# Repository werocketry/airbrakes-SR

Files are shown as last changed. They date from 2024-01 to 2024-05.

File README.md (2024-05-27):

# airbrakes-SR

This is the repository for the Western Engineering Rocketry Team's design of an airbrakes system.

## Sister Projects

- [werocketry/RocketFlightSim](https://github.com/werocketry/RocketFlightSim)
- [werocketry/HPR-Rocket-Flight-Computer](https://github.com/werocketry/HPR-Rocket-Flight-Computer)

## Acronyms of the Trade
| Acronym | Full Name | Description |
|---|---|---|
| AGL | Above Ground Level | |
| COTS | Commercial off-the-shelf | |
| CP | Center of pressure | |
| ESRA | Experimental Sounding Rocket Association  | |
| FOS | Factor of Safety | |
| FS | Factor of Safety | |
| IREC | Intercollegiate Rocket Engineering Competition | Basically SAC. It used to happen somewhere else |
| NM | New Mexico | |
| NMSU | New Mexico State University | The university on whose grounds some parts of SAC are held |
| OR | OpenRocket | |
| .ork | OpenRocket filetype | |
| RSO | Range Safety Officer | The person that gives you permission to launch |
| SA | Spaceport America | The launch site where SAC is hosted |
| SAC | Spaceport America Cup | |
| SRAD | Student researched and designed | |
| VLA | Vertical Launch Area | |
| WERT | Western Engineering Rocketry Team | Also called WE Rocketry |

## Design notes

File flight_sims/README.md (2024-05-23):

# Flight Analysis

Flight simulations, analysis of Prometheus' flight data

- **Alignment of Sim Data with Experimental Data:** 
  - About 1000 ft off around motor burnout.
  - try taking data to motor burnout and simulating remainder of flight to see congruence with experimental data
    - just run sim as is and set deployment angle to 0 for the entire flight
  - this isn't a real problem; it's caused by the delay in barometric sensor data. The rocket should have been just about where the sim says it would be at motor burnout, it's just a delay on the order of 0.8s in the pressure in the rocket getting to equilibrate with the pressure outside the rocket that causes the discrepancy.
  - Note that if wanting to simulate airbrakes using Prometheus experimental data as the data till burnout, the flight data has no vertical vs horizontal velocity data, so would need to use the speed and change of height with time to separate them out. Possibly use the velocity not being 0/the acceleration not being -g at apogee to help determine the horizontal motion then too. Not a priority at all.

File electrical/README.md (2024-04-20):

# Electrical 
TODO

## Future Work
### Electrical Hardware Revision

Future work will also focus on the revision of the electrical hardware,
namely the manufacture and testing of the printed circuit board for the
presented Production Prototype version of the electrical system.

### Flight Computer Development

As the development of a complete flight computer is a large undertaking,
future development is required to satisfy this component. The team will
work closely with the sponsor to ensure that our development efforts run
parallel to their future development of SRAD flight computers.

### Software Integration

The core software components of the system presented complete herein
still require careful development and planning for their integration
into a single standalone program capable of running this entire complex
system.

### Model-Based Control for Drag Modulation

The current mechanism controller uses a look up table calculated offline
to determine the motor action required to produce the desired drag.
Future work will focus on the use of a Model Prediction Control
algorithm which uses an internal model of the rocket to predict the path
and actively mitigate deviations from the desired path in the presence
of external disturbances.

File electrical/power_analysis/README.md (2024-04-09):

The power supply for the project relies on Lithium-ion (Li-ion) batteries, selected for their high energy density and efficiency. The choice of Li-ion batteries was heavily influenced by competition rules that explicitly ban the use of Lithium Polymer (LiPo) batteries \[4\] and our research showed that this is a common alternative used in the SAC competition. In selection of the battery cells the capacity, max discharge rate, and voltage requirements were considered. The power consumption ratings for each of the relevant components is given in Table 1.

**Table 1: Power Consumption of Relevant Electrical Components.**

| Component | Electrical Power | Details |
|---|---|---|
| Portenta H7 | 2.6 mA @ 3.7V | Current consumption in busy loop (@5V) \[max with on board LEDs off\]. |
| Nicla Sense ME | 2.5 mA @ 3.7V | Power consumption advertising with sensor polling at 1Hz \[max consumption state\]. |
| L298N Motor Driver (VEN=L)  | 4 mA @ 12V<br>6mA @ 5V | Quiescent supply & VSS current of inactive driver \[max value of range taken\]. |
| L298N Motor Driver (VEN=H)  | 22 mA @ 12V<br>36 mA @ 12V | Quiescent supply & VSS current of active driver \[max value of range taken\]. |
| Brushed DC Motor | 5000 mA @ 12V | Stall current of the selected motor. |
| Hall Effect Sensor | 6.9 mA @ 5V | Supply current of the IC. |

To calculate the required capacity, the 20-hour required standby time given in ER-003 and an active motor time of 10 seconds (approximately a FOS of double the predicted motor action time. This yields a total required capacity of approximately 400 mAh, the calculations are broken down in Table 2. The datasheet for the Arduino Portenta recommends a greater minimum of 700 mAh for battery powered use and this will hence be used as the single cell minimum herein.

**Table 2: Energy Requirement Breakdown.**

| Phase | Component | Current (mA) | Voltage (V) | Active Time | Energy Required (mAh) |
|---|---|---|---|---|---|
| Standby | Portenta H7 | 2.6 | 3.7 | 20h | 52 |
| | Nicla Sense ME | 2.5 | 3.7 | 20h | 50 |
| | L298N Motor Driver | 6 | 5 | 20h | 120 |
| | Hall Effect Sensor | 6.9 | 5 | 20h | 138 |
| Standby Subtotal | | | | | 360 |
| Active | Brushed DC Motor | 5000 | 12 | 20s | 27.78 |
| | L298N Motor Driver (Active) | 36 | 12 | 20s | 0.2 |
| Active Subtotal | | | | | 27.98 |
| **Total Required Energy** | | | | | 387.98 |

The MCU board is supplied with by a single 3.7V cell which the onboard regulator regulates to 5V to power the 5V components. The DC motor is rated at 12V therefore 3 cells are required to reach the required potential which results in a nominal 11.1V (within 10%). As the cells will be wired in a 3 series (3S) configuration each must independently be capable of supplying the maximum current of the motor, that is 5000 mA which sets the required minimum discharge current.

This gives a selection criterion of three cells rated at least 700 mAh each with a minimum discharge rate of 5000 mA. The Panasonic NCR18650GA 3450mAh 10A Battery was chosen for this application as it meets and exceeds these required specifications while remaining well within budget. It's important to note that most modern lithium-ion cells, even those that are more affordably priced, meet or exceed the required specifications for this project making the exact product selection rather arbitrary. Therefore, the specific selection of the product was primarily driven by the reputable brand name, price point, and supplier accessibility. The power to the microcontroller uses the same model of low-power switch as for the user input and the power switch to enable power to the motor circuit is a power switched rated up to 6A.

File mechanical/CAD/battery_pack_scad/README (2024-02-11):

https://www.amazon.ca/0-15x6x50mm-Soldering-Capacity-Lithium-Battery/dp/B07PQP55CM?th=1

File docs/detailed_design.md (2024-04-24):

# Detailed Design

## Mechanical Design

After the transition to three flaps in January, the basic mechanical
design has remained largely unchanged, barring a few minor, yet
necessary, adjustments identified through the mechatronic model. The
initial modification involved adding washers at both ends of the lead
screw, addressing rough edges (burrs) left from the lathe-milling
process. To accommodate the lead screw\'s turned-down smooth shaft, and
ensure an effective interface with the bronze bearing, two precision
tolerance washers from McMaster-Carr were selected, as detailed in
Figure 13. Another revision was the development of a motor mount. The
integration of electronic components revealed the absence of a suitable
motor mounting solution on the top platform and lead screw. To solve
this, a component that attaches to the top platform was designed,
providing a robust mount for the motor and facilitating the coupler
connection to the lead screw, depicted in Figure 16.

The third modification entailed adding three \"platform spacers\" to
maintain the critical distance between the two platforms, which directly
influences the compression on the lead screw. Too little distance
results in binding due to the lead screw pressing against the platforms,
while too much distance introduces unwanted play in the mechanism. The
incorporation of these spacers, firmly secured with screws, ensures the
correct spacing is consistently maintained, highlighted in blue in
[]{.mark}Figure 14. This approach was deemed suitable as it had been
effectively tested in the 3D-printed mechatronic model and the
airbrake\'s weight budget comfortably accommodated the additional mass.

Initially, the correct spacing was to be achieved by first installing
the top platform, measuring the appropriate distance, then fitting the
remainder of the system. However, recognizing the potential for
variability in this method, it was decided to include platform spacers
to allow for one-piece installation, enhancing precision and
reliability.

Subsequent adjustments were made to the flap dimensions, following the
WE Rocketry Team\'s recommendation for slightly larger flaps. This
necessitated minor modifications to maintain the correct part
relationships, preserving the mechanism\'s fundamental operation as
established in previous iterations.

Finally, the integration of electronics prompted the addition of Hall
Effect sensors to determine the system\'s limits, requiring alterations
to accommodate sensor boards on the top and bottom platforms and the
installation of magnets on the lead nut. These changes, though minor,
were crucial for the precise functioning of the mechanism, illustrated
in Figure 15.

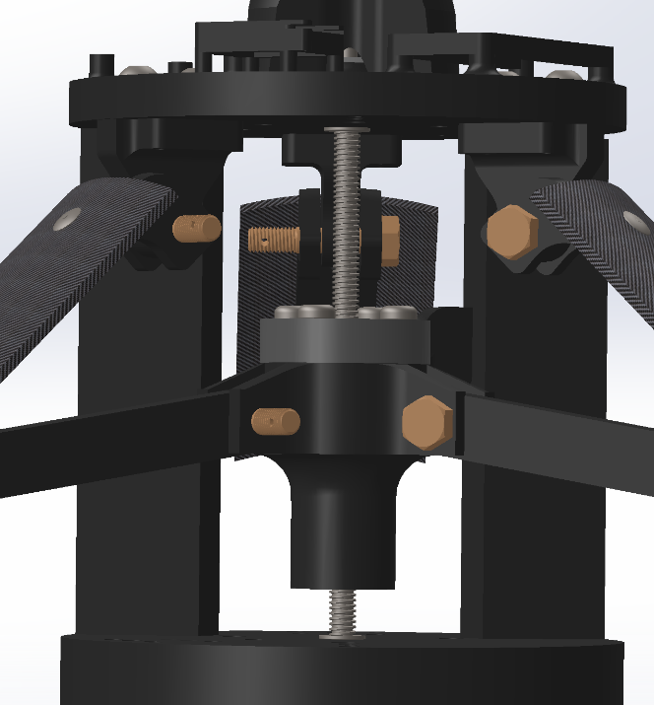
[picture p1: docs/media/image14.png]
A black machine with metal parts Description automatically generated

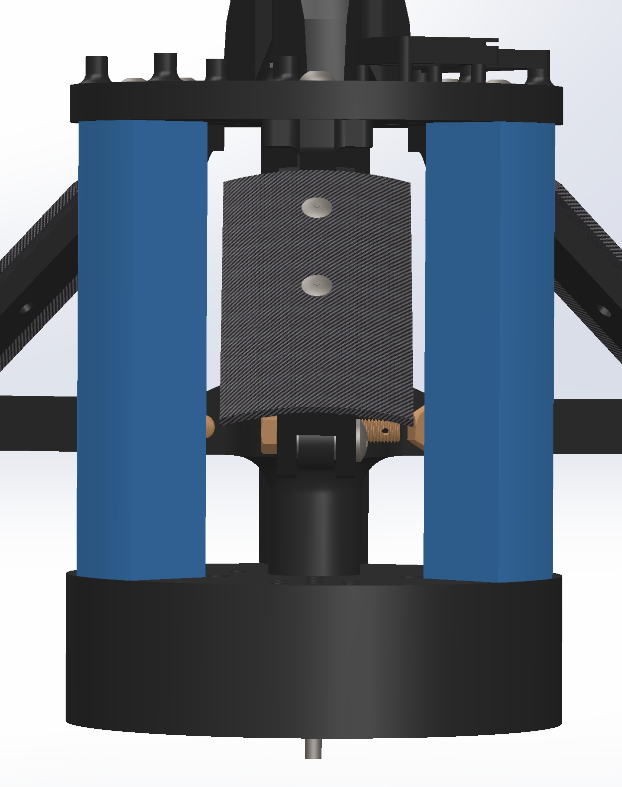
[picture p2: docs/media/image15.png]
A close up of a machine Description automatically generated

  ----------------------------------------------------------------------------------------------------------------------------------------------------
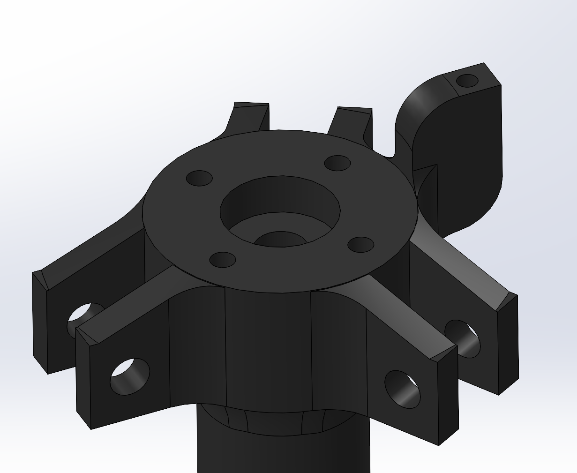
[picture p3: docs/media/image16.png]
A black object with holes Description automatically generated
  ![A black metal object with holes Description automatically               {width="2.611408573928259in"   generated](./media/image17.png){width="2.4880949256342957in"
  height="2.1404636920384954in"}                                            height="2.1489063867016625in"}
  ------------------------------------------------------------------------- --------------------------------------------------------------------------

  ----------------------------------------------------------------------------------------------------------------------------------------------------

  : []{#_Ref163390546 .anchor}Figure 1: Rocket with airbrakes: surfaces
  controlled by a servomotor which can increase the longitudinal drag
  forces. The airbrakes are located behind the center of pressure to
  guarantee stability.

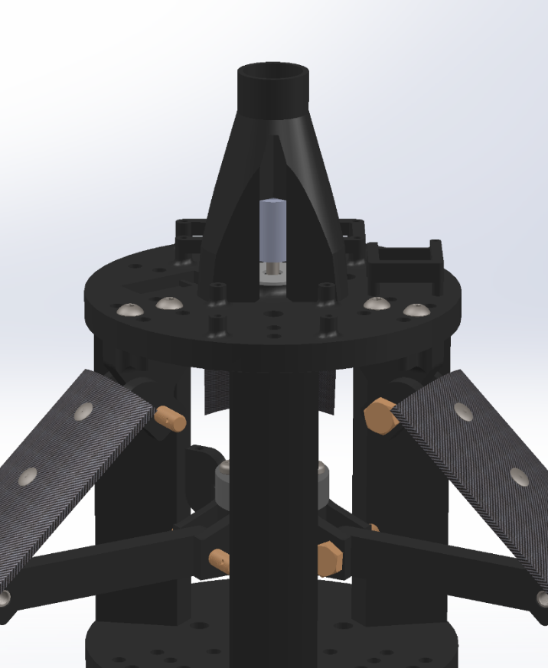
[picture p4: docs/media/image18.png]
A black object with metal parts Description automatically generated

## Mechanical Material Selection

### 3D Printed Components

When looking at the materials selected there is an apparent strong
emphasis put on 3D-printed parts. This was a decision made with a
considerable amount of deliberation as 3D-printed materials are often
"unknown" or "lesser-known" in their specific performance factors.
Clearly this can make the accurate representation of materials in FEA
more complicated and can make the material validation process laborious
when compared to commonly used/studied materials (ex. Aluminum).

To briefly go over some of the factors considered when making this
important decision the first and likely most important is the background
research. Fortunately, since 3D-printing is a relatively new topic in
engineering it is being extensively studied and there is seemingly a
sufficient body of material to obtain a fair FEA material profile from.
Four studies were compared \[16\], \[17\], \[18\], \[19\] when
determining what values would initially be used for the PLA material
profile. After using the lowest values listed in these studies a
material profile was then constructed allowing for the start preliminary
FEA on the parts. Furthermore, it is well know that 3D-printed parts are
strong in compression, but weak in tension due to layer line adhesion
\[20\] (when the layer lines are normal to tensile direction).
Therefore, even when the preliminary FEA determined our parts were
strong enough, the precaution of layer orientation was also taken into
consideration to ensure that the parts were likely even stronger than
the FEA results would indicate.

Once the parts had been printed and assembled, they were subjected to
the expected loads of the airbrake system based on our simulation
results. The test showed that the 3D-printed parts would not deform
elastically or plastically under the expected loads and no obvious forms
of wear including damage or cracking were observed in the components.

The final factor taken into consideration is the opinion of the team's
faculty supervisor Dr. Makaran. Early on, when discussing material
selection Dr. Makaran was consulted for his opinion on using 3D-printed
parts in the design. Once Dr. Makaran was informed of the loads the
components would be subjected to, he too reassured the team that to his
knowledge 3D-printed parts would work, but he urged the team to still
continue investigating and to do the physical tests that were discussed
earlier.

### Carbon Fiber Parts

Since the early stages of the project the flaps were designed to be
carbon fiber mainly due to their strength and weight properties.
Initially the flaps were planned to be forged carbon fiber, manufactured
using a compression mold. However, after initial manufacturing testing
of this process it was determined that the process was too complex for
the scope of the project and the end result was not satisfactory. The
manufacturing testing results lead to the initialization of a material
re-selection process for the flaps.

After careful consideration, woven carbon fiber was chosen due to a
multitude of factors. Primarily, the team could cut the flaps out of
pre-manufactured tubes that the Rocketry team has, ensuring that the
curvature of the flap directly matches the tube it is mounted in.
Furthermore, since the rocketry team has been manufacturing these tubes
for many years the properties of the carbon fiber is well established
and the quality of the parts is sufficient. No other carbon fiber parts
were used as the manufacturing process is labour intensive and was
deemed to be unnecessary for the scope of this project and its use case.

### Off-the-Shelf Components

All purchased items were sourced from McMaster-Carr due to their large
selection and fast shipping times. All components purchased from
McMaster-Carr were specifically chosen to fit the needs of the project
while still attempting to be commonplace items, so as to reduce the
number of custom parts needing to be machined in the future. All
fasteners involved in the linkage mechanism were chosen due to their
"un-threaded" length which allowed for them to act as the hinges and
keep the design simple. Furthermore, low-profile barrel screws were
chosen for the lower hinge mechanism to maintain a similar hinging
methodology as the other fasteners, while having a low profile to
accommodate for the space constraints in this area.

The center lead screw was chosen after significant deliberation between
the mechanical and electrical systems to optimize the number of
rotations needed between the stowed position and fully deployed
position. Three options of TPI were assessed and the one found to be
most well suited for the project was the ¼-12 lead screw. This lead
screw was a fair balance between cost and travel per revolution. It was
determined that for this lead screw 25.38 revolutions would be needed as
the distance traveled by the lead nut is 2.10" and the TPI is ¼-12. A
requirement from electrical systems was that the revolutions be kept
below 28 and this TPI accomplished this. As mentioned previously, other
TPI's were considered including ¼-20 as it is an industry standard but
did not satisfy the \< 28 revolution requirement, and the ¼-8 TPI also
considered was too expensive to justify.

Two specific types of washers were purchased for this project. The first
was a high-tolerance machined washer, chosen to fit over the machined
section of our lead screw and provide a sacrificial interface between
the ends of the lead screw threads and the platform bushing. The second
type of washer chosen was a mil-spec thin washer. This washer was chosen
to provide a low-friction replaceable surface for the hinges to rub on,
while also eliminating the lateral play in the hinges that was
intentionally designed to accommodate for the fact that the parts were
going to be 3D-printed.

All other purchased components were minor components and were chosen to
be very common sizing (ex. ¼-20 bolts) as to not necessitate a
McMaster-Carr order but were added to the teams purchase order to
simplify our material purchasing process.

## Computational Fluid Dynamics (CFD)

CFD simulations are used in the design phase of the airbrakes system to
analyze and understand the complex aerodynamic behaviour and flow
patterns around the system. For the purposes of the Capstone project
deliverables, CFD studies were conducted on the rocket structure without
the airbrakes deployed. These preliminary studies were conducted for the
following reasons:

### Baseline Comparison

The CFD simulations without the airbrakes were used to establish a
baseline understanding of the aerodynamic behaviour of the rocket. This
baseline provides insight into the rocket's normal operational state
without the influence of the airbrakes. It provides a clear starting
point for comparison of the drag forces when airbrakes are later
introduced. Additionally, most of the drag force is produced by the
rocket rather than the airbrakes. Therefore, these studies provide a
good picture of the whole flight despite a precise prediction of the
drag induced by the airbrakes.

Through predicting the rocket's aerodynamic performance without
airbrakes, factors such as drag coefficients can be understood under
various operating conditions. These predictions serve as a reference for
evaluating how the introduction of airbrakes will impact overall vehicle
performance.

### Computational Efficiency

Conducting initial CFD simulations without the airbrakes allows the team
to streamline the computational process and optimize simulation
parameters such as mesh resolution, turbulence models, and boundary
conditions. This is important for reducing computational time and
resources for future complex simulations.

The CFD simulations performed used a mesh resolution of 0.05 mm and
inflation layers along the rocket's external structure to better resolve
the boundary layer. The boundary conditions included an inlet with a
specified velocity, a 0 Pa pressure outlet, and walls with specified
shear of 0 Pa to represent an infinite domain. The turbulence model used
was the k-omega shear stress transport because the flow around the
rocket is expected to separate at high velocities, and this turbulence
model is most accurate at simulating the detachment of the boundary
layer \[21\].

The results from the CFD simulations are currently preliminary. Future
CFD simulations are warranted to determine the influence of the
airbrakes on the drag forces. However, research indicates that the drag
induced by the airbrakes has been shown to be relatively decouplable
from the rest of the rocket's drag and many teams have determined that
airbrakes have a drag coefficient of 1.0 \[22\]. The custom simulator
uses this information presently as an input. The future CFD simulations
will provide updated values to be included in the custom flight
simulator.

## Flight Dynamics

Understanding of the flight dynamics informed many design decisions. Due
to the importance of accurately knowing how the rocket would perform
during flight and how airbrakes would alter the flightpath of the
rocket, several methods were used to analyze flight dynamics. Some of
the most important factors that influenced the design which can be
determined from an accurate representation of the flight dynamics are:

1.  A determination of the maximum g-force that the rocket -- and thus
    the airbrakes system -- is expected to be subjected to during
    flight.

2.  A determination of the aerodynamic pressures that airbrakes are
    expected to experience during flight.

3.  A projection of the maximum extent to which drag induced by the
    airbrakes system could change the rocket's apogee.

4.  An estimation of the maximum force that the airbrakes flaps would
    experience if they were to deploy as quickly and as early as
    possible.

### Custom Simulation

One key tool used to make design decisions, which is also used by the
airbrakes controller, is a custom-made flight simulator, coded by the
team in Python. The full simulation can be accessed on the team's
GitHub, and visualizations of the simulation results can be found in the
file visualizations.ipynb. Key figures for this report determined by the
simulation are shown below in Table 5:

  -----------------------------------------------------------------------
  Figure                                        Value
  --------------------------------------------- -------------------------
  Apogee without airbrakes deployment           11745 ft (3580 m)

  Apogee with maximum airbrakes deployment      9977 ft (3041 m)

  Maximum g-force                               13.58 g

  Max-q on rocket                               49.63 kPa

  Maximum force on a flap                       32.5 N
  -----------------------------------------------------------------------

  : []{#_Toc163515992 .anchor}Figure 2: ARAC model in fully closed state
  (left), Isometric view of ARAC model in max extension state (right).

In accordance with FR-002, the airbrakes as simulated can induce enough
drag to reduce the rocket's apogee to within 200 ft of its 10 000 ft
target to achieve our goal. Figure 17 and Figure 18 give a visualization
of how the simulated flightpaths differ between when airbrakes are not
deployed (Figure 17) versus when the airbrakes are deployed as fast as
they can be (and then remain fully deployed for the duration of the
flight, in Figure 18).

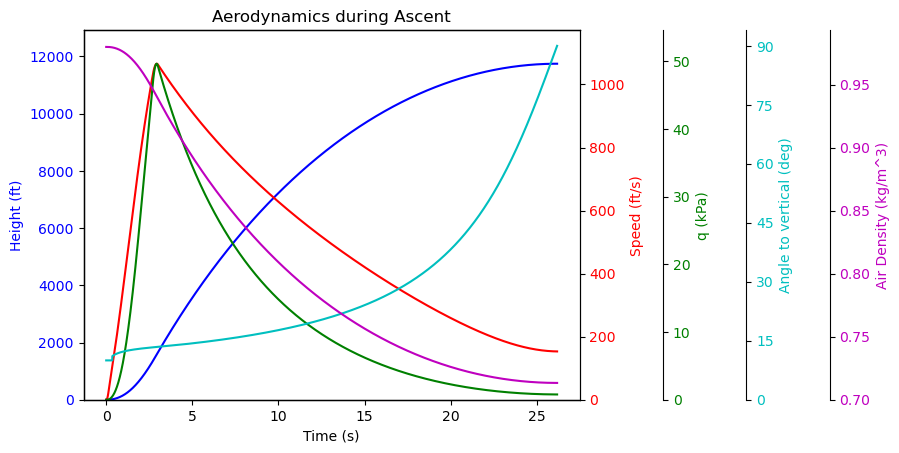
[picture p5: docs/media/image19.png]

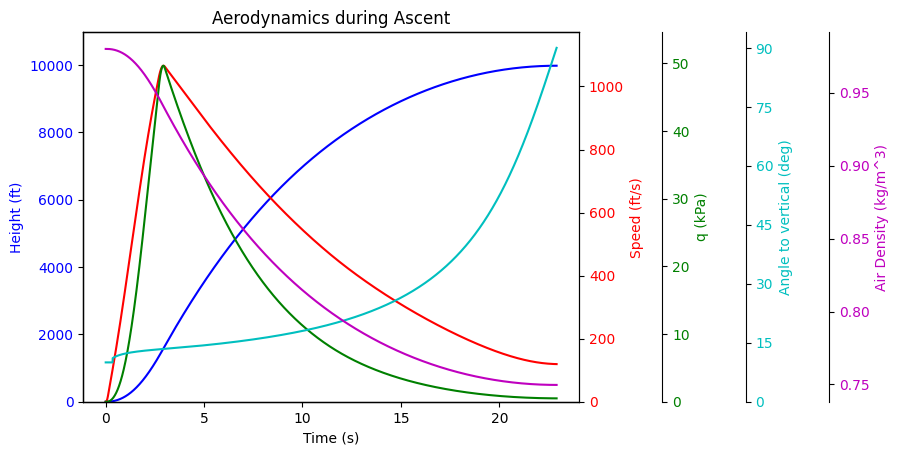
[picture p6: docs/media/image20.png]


It should be noted that as of the publication of this report, the mass
budget of the rocket is in a state of flux as some final design
considerations are still being made by the rocketry team's various sub
teams, and some final parts are still being fabricated. Depending on
when this report is read, the most up-to-date version of the
aforementioned "visualizations.ipynb" may have updated values that are
different than those reported in the table and figures above.

### OpenRocket Simulations

OpenRocket simulations were conducted in collaboration with WE
Rocketry's propulsion sub team. Their results help validate the custom
flight simulation created by the airbrakes team. Several OpenRocket
simulations were performed on a range of different possible wind
conditions to get a more wholistic view of what conditions the rocket
might experience during flight. For the purposes of this report,
worst-case scenarios of the maximum g-force and max-q as reported in
Table 7 come from the OpenRocket simulation without any wind (as it is
with no wind that those parameters are at their largest).

### RocketPy Simulations

A further series of simulations were run using RocketPy, which released
an update allowing for airbrakes simulation in February. The values
obtained from the simulation align very well with those obtained from
the custom simulation and can be found in Table 7.

### Bounding Calculations

The absolute worst-case scenarios, assuming no parts of the rocket
unexpectedly come off, can be determined with simple calculations as
follows. These calculations are a good way to check if the values
determined using the methods in the previous sections are reasonable.

The maximum g-force that the rocket could experience (assuming it
remains intact during its ascent) is bounded by three parameters: the
motor's thrust curve, the rocket's mass, and the force of gravity.
Assuming there to be absolutely no drag is unrealistic, but doing so
provides a ceiling on the maximum possible g-force, that can
conveniently be determined in a few minutes according to Equation 1:

$$F_{g\ max} = \frac{F_{thrust\ max}}{m_{rocket\ dry} + m_{fuel}(t = t\left( F_{thrust\ max} \right))} - g$$

The inputs to Equation 1 are summarized below in Table 6:

  -----------------------------------------------------------------------
  Parameter                           Value
  ----------------------------------- -----------------------------------
  Maximum thrust force of the         2938 N
  Cesaroni 7450M2505-P motor \[23\]   

  Dry mass of the rocket              17.963 kg

  Mass of fuel remaining in the       1.982 kg
  Cesaroni 7450M2505-P motor at the   
  time of maximum thrust (1.2s)       
  \[23\]                              
  -----------------------------------------------------------------------

  : []{#_Toc163515993 .anchor}Figure 3: Underside view of ARAC system
  near max extension; linkage mechanism identified.

Given the values in Table 6, Equation 1 yields a maximum g-force on the
rocket of 14.02 g.

Similarly to how an upper bound on the max-g force was calculated, an
upper bound on max-q can be calculated assuming no drag to help validate
the results of the simulations. Once again, it is an upper bound that,
given the rocket's parameters and that it does not fall apart during
ascent, cannot physically be reached. The upper bound can be calculated
by first finding the maximum velocity which the rocket can attain if it
didn't experience any drag, using Equation 2:

$$v_{\max} = \max\left( \int_{0}^{t}{\left( \frac{F_{thrust}\ (t)}{m(t)} - 9.81\frac{m}{s^{2}} \right)\ } \right)$$

Where the t in the integral ranges from 0 to the time of motor burnout.

Using the thrust curve and fuel burn rate of the Cesaroni 7450M2505-P
motor \[23\] and the dry mass of the rocket (as reported in Table 6),
the maximum velocity the rocket could theoretically attain is 342.1 m/s.
Using this value and taking the worst-case value for air density as the
air density at the launchpad (0.98 kg/m^3^)[^1], an upper bound for the
aerodynamic pressure that the rocket cannot physically reach can be
calculated using Equation 3:

$$q = \frac{1}{2}*\rho*v^{2}$$

Plugging in the aforementioned values into Equation 3 gives an upper
bound on the aerodynamic pressure of 57.34 kPa.

### Summary and Comparisons

The results of the different simulations and bounding calculations are
well-aligned. Comparisons of the four methods are summarized below in
Table 7:

  ----------------------------------------------------------------------------
  Method         Maximum   Max-q (kPa)  Apogee - no        Apogee - max
                 g-force                airbrakes          airbrakes
                 (g)                    deployment (ft)    deployment (ft)
  -------------- --------- ------------ ------------------ -------------------
  Custom         13.58     49.63        11745              9977
  Simulator                                                

  OpenRocket (no 13.47     47.00        10469              \-
  wind)                                                    

  RocketPy (no   13.56     53.8         11880              10078
  wind)                                                    

  Bounding       14.02     57.34        \-                 \-
  Calculations                                             
  ----------------------------------------------------------------------------

  : []{#_Toc148736783 .anchor}Figure 4: EULER full-body CFD: pressure at
  Ma 1.2.

### Stopping Power Analysis

To determine the size of flaps that would be necessary to provide enough
stopping power to bring the rocket's final apogee down to 10 000 ft, a
sensitivity analysis was conducted using the custom flight simulator.
The analysis considered what the simulated apogee would be at different
deployment speeds and with different flap sizes, assuming that the
airbrakes deployed to their full deployment angle as fast as possible
and remained fully deployed for the duration of the flight (giving the
maximum possible drag that airbrakes with that specific deployment speed
and flap size could produce).

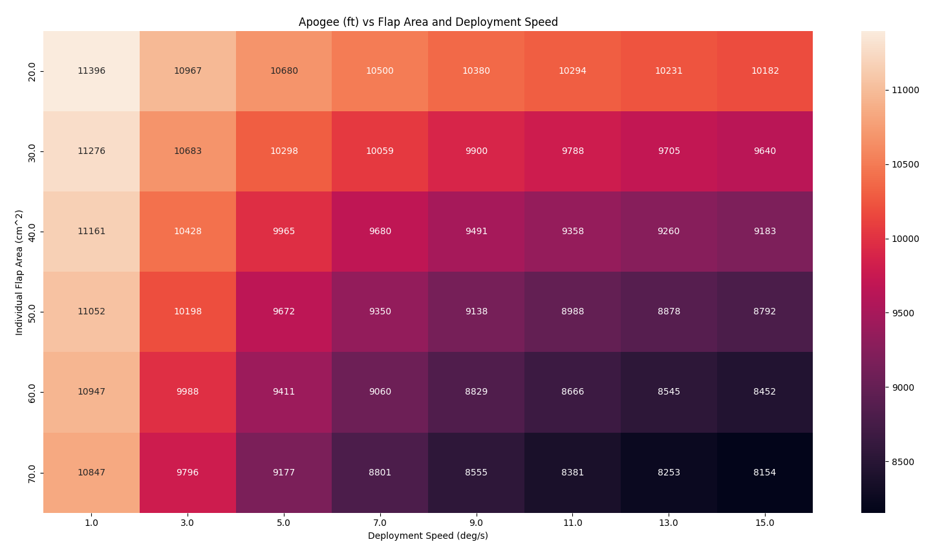
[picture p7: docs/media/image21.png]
A color palette with different shades of red and orange Description automatically generated

## Electrical Design

The electrical design presented herein is scoped into two versions or
phases of development to align with the stakeholders' requirements. The
first phase is the completed Functional Prototype (FP) to enable the
validation and verification of the overall system design and will hence
be flight-ready, but non-optimized. The second phase is the Production
Prototype (PP) which is focused on refining the design for
manufacturability and efficiency, transitioning from a functional
prototype to a streamlined version suitable for limited production runs
by future teams as they iterate and improve upon the design. This second
phase includes developing a custom Printed Circuit Board (PCB) and
redesigning certain components initially sourced as off-the-shelf
modules to create an integrated solution that aligns with industry
standards.

### System Overview

The electrical system consists of five major parts: 1) the
microcontroller development board, 2) the motion and environment sensor
array, 3) the motor circuit, 4) system sensors, and 5) the power supply.
The sensor array obtains information on the motion of the rocket and its
external environment which is read by the microcontroller along with
information obtained from the system sensors on the internal state of
the mechanism to determine actuation of the motor circuit. The FP
electrical schematic is shown in Figure 20 with the major parts
indicated. Individual figures for each of the blocks are given in
Appendix II for easier in-depth viewing.

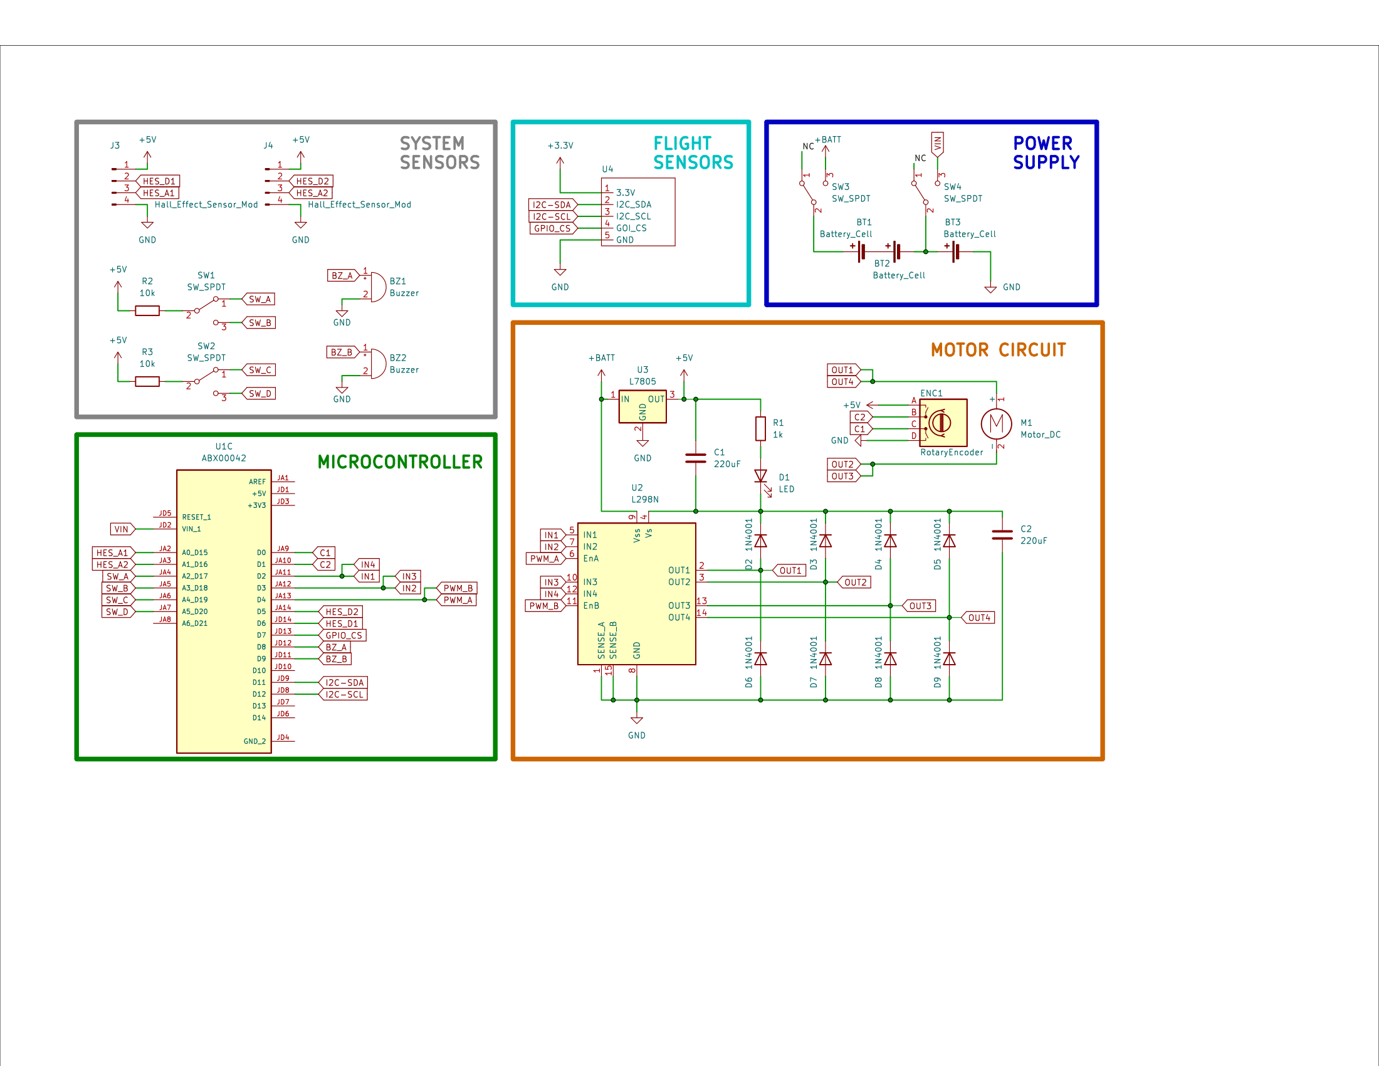
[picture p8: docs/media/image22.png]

### Load Analysis & Motor Selection

This method and results of this analysis section can be accessed on the
team's GitHub
([link](https://github.com/chasgior214/airbrakes-capstone/tree/main)).
The force-torque analysis began with converting the mechanical geometric
of the leadscrew push-rod mechanism into a static mechanical model.
Figure 21 displays a stripped down and highlighted version of the
mechanical model to only show the essential components of the problem.

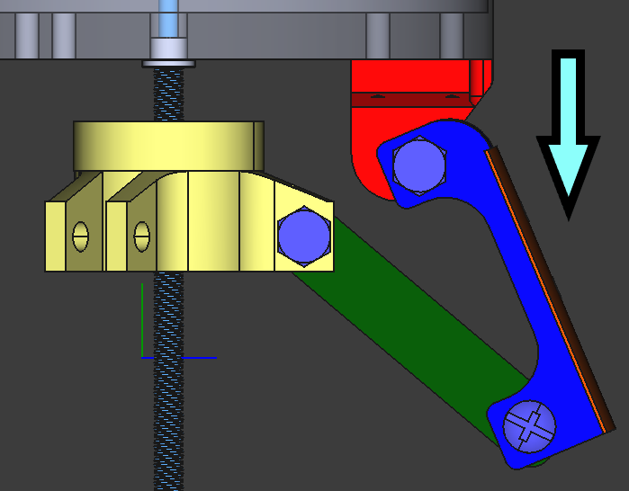
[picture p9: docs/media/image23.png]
A blue red and yellow metal object with a blue and green line Description automatically generated with medium confidence


The simplicity of the mechanism allowed it to be readily converted into
a simple two-force member model diagram in which to solve, shown in
Figure 22. The force in the model is applied normally as it represents
the equivalent aerodynamic load considering the deployment angle, that
is, sine of theta. The aerodynamic load considered was a
worse-case-scenario of the highest of the calculated q-max values (56.21
kPa) at full deployment (41.35°). It is directed at the midpoint of
member CD since it assumes an even distribution of force across the
length.

  -----------------------------------------------------------------------------------------------------------------------------------------------------
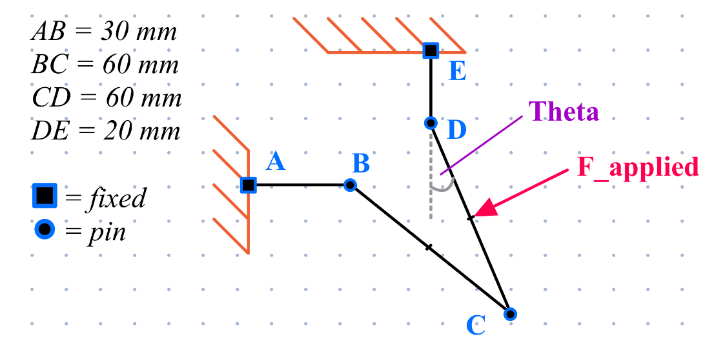
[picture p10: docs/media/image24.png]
A diagram of arrows pointing to a square Description automatically generated
  ![A diagram of lines and arrows Description automatically                  {width="3.2395833333333335in"   generated](./media/image25.png){width="1.4919674103237095in"
  height="1.596392169728784in"}                                              height="1.5958333333333334in"}
  -------------------------------------------------------------------------- --------------------------------------------------------------------------

  -----------------------------------------------------------------------------------------------------------------------------------------------------

  : []{#_Toc148736784 .anchor}Figure 5: EULER full-body CFD: fin
  interaction.

The force can be decomposed into its components using the known theta
angle, this force will be equally shared between the two pins and then
the force can be simply passed along the members assuming static
equilibrium. As shown in Figure 22 the forces being exerted by the lead
screw nut on the push rods is down and inwards as expected. Python was
used as the numerical solver for the analysis which also included a
factor of safety for uncertainties and inefficiencies such as friction
and imperfections. The resultant forces based on the described analysis
yielded -59.28 N in the x-coordinate and -23.95 N in the y-coordinate.

The efficiency of the lead screw was calculated using a python script
which took into account the physical and material characteristics of the
screw and nut assembly based on the manufacturer provided
specifications. The pitch diameter is assumed to be approximately equal
to the nominal diameter of the screw. Subsequently, the lead angle is
determined using the formula:

$Lead\ Angle = \ \tan^{- 1}\frac{Lead}{\pi\  \times Pitch\ Diameter}$
(5)

which assesses the angle made by the thread\'s helical rise relative to
the screw axis. The angle of friction, dependent on the materials\'
coefficient of friction, is calculated using:

$Angle\ of\ Friction = \ \tan^{- 1}{(Coefficient\ of\ Friction)}$ (6)

The final step involves computing the efficiency of the lead screw,
which is a measure of the mechanical advantage versus the energy lost
due to friction. This is done using the formula:

$Efficiency = \ \frac{tan(Lead\ Angle)}{tan(Lead\ Angle + Angle\ of\ Friction)}$
(7)

The efficiency result was 22.13%, which falls within the expected range
for the Forward Drive Efficiency of an Acme Lead Screw for the given
dimensions \[24\].

The efficiency of a lead screw, previously calculated, was applied
alongside the expected load from a static mechanics model to determine
the load torques for both driving and holding. For the driving torque,
the equation is given by:

$Driving\ Torque = \ \frac{Load\  \times Lead}{2\pi\  \times Efficiency}$
(8)

This calculation involves the load (in pounds), the screw lead (in
inches per turn), and the screw\'s efficiency, with the torque expressed
in pound-inches. The holding torque, indicative of the force needed to
keep the load stationary, is derived using the equation:

$Holding\ Torque = \ \frac{Load\  \times Lead \times Efficiency}{2\pi\ }$
(9)

The resulting maximum required driving torque is 1.14 kg-cm and the
required holding torque is 0.08 kg-cm. Going forward into the motor
selection the required driving torque was used to continue tending to
the worse-case-scenario.

To evaluate the required torque of the expected scenario, the force
profile obtained in the flight dynamics analysis is fed into the
load-torque analysis to obtain the torque curve seen in Figure 23Figure
23. Based on the required number of rotations required for the
deployment of the mechanism (25.38 rotations) and the estimated
deployment time from the flight dynamics analysis (8.18 seconds) the
required speed can be calculated to be approximately 186 RPM. In
preparation for motor selection additional calculations were written to
obtain the motor requirements in various units and conventions to aid in
components sourcing and are included in the analysis script.

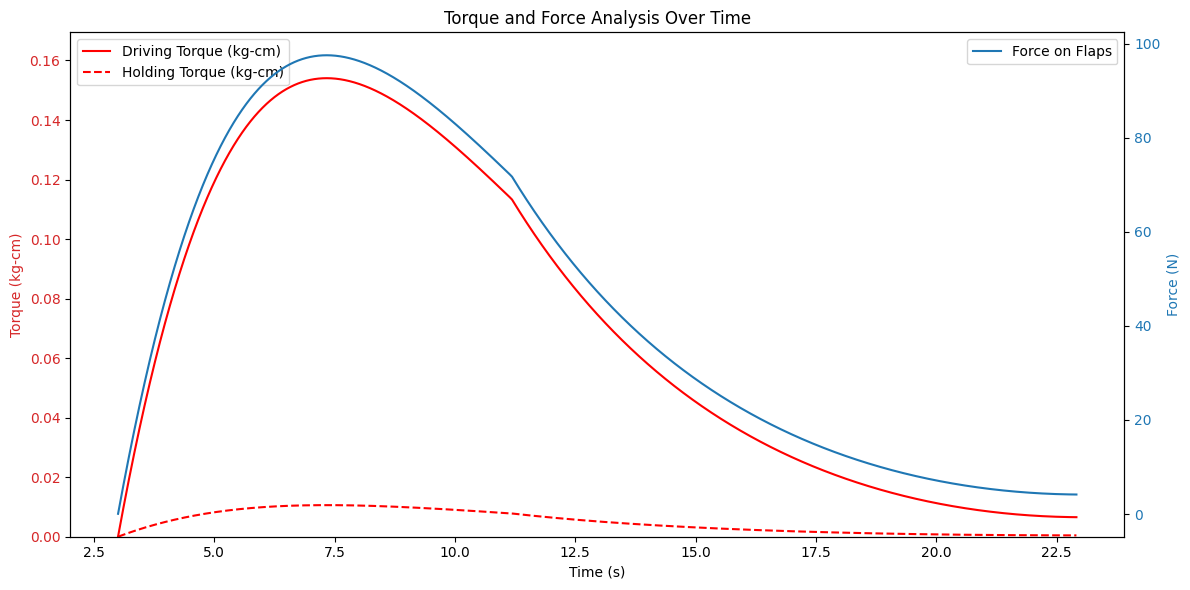
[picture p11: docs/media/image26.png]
A graph of a person and person Description automatically generated with medium confidence

Based on the given requirements a 20mm 12V Planetary Gearmotor with an
Encoder was selected, the specifications of which are in Table 8.

  -----------------------------------------------------------------------------
  **Component**   **Dimension/Specification**   **Value/Description**
  --------------- ----------------------------- -------------------------------
  *Gearbox*       Diameter x Length             20D x 21.5L mm

  *Motor*         Diameter x Height x Length    20D x 14H x 32L mm

  *Shaft*         Diameter x Length, Shape      4D x 10.5L mm, D-shaped

  *Encoder*       Type, channel number, pulses  Magnetic encoder, 2 channels,
                  per rotation                  11PPR

  *Model*                                       20PG-180SH-29-EN 12V

  *Electrical*    Voltage                       12V DC

                  Reduction Ratio               1:29

                  No-load Speed                 515 RPM

                  No-load Current               \< 280 mA

                  Rated Torque                  0.65 kg.cm

                  Rated Speed                   445 RPM

                  Rated Current                 \< 550 mA

                  Stall Torque                  \> 3 Kg.cm

                  Stall Current                 \< 2.7 A
  -----------------------------------------------------------------------------

  : []{#_Toc148736785 .anchor}Figure 6: The ThrustMIT Airbrake system in
  both the stowed and deployed positions.

The selection of a brushed DC motor for the project was guided by
several critical design requirements. Firstly, the application\'s need
for unconstrained rotation eliminated servo motors, which are typically
limited in their rotation capabilities. Additionally, the project\'s
stringent mass constraints necessitated a motor with a high-power
density, ruling out stepper motors due to their generally lower
power-to-weight ratio. Furthermore, the project\'s specific electrical
complexity and performance requirements deemed brushless DC (BLDC)
motors excessive for the intended application. Consequently, a brushed
DC motor, augmented with a gearhead, was identified as the optimal
choice. The gearhead effectively adjusts the motor\'s torque and speed
characteristics to align with the expected load conditions. Moreover,
the integration of an encoder enables precise closed-loop feedback on
the mechanism\'s position, ensuring the desired level of control and
performance.

The specific motor selected meets the system requirements as it will be
operating in the 10-30% range (\~0.15 kg-cm operating to 0.65 kg-cm
rated) of the rated torque which will place the required speed firmly
within the acceptable range for pulse-width modulation control (155 RPM
operating to 445 rated).

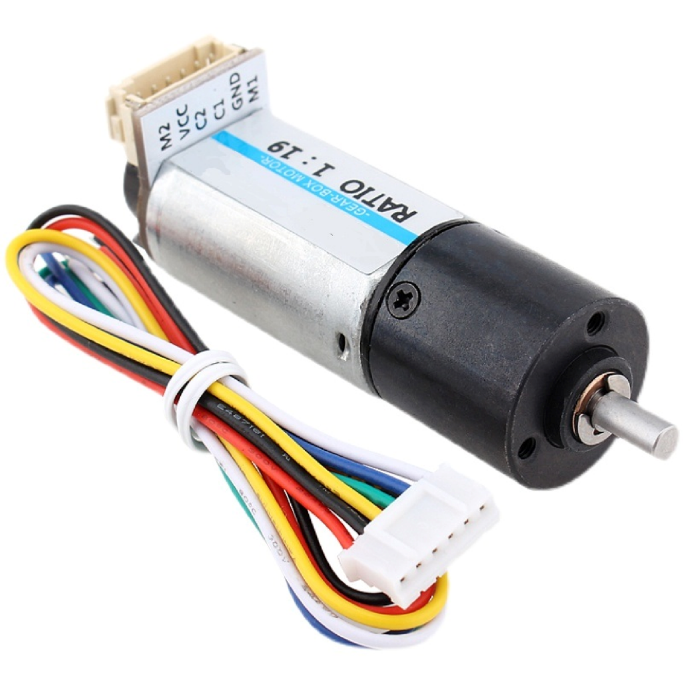
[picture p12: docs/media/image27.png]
A small electric motor with wires Description automatically generated

### Motor Driver Circuit

The motor circuit consists of the selected brushed DC motor driven by
the L298N full bridge breakout module. This was selected as it is widely
used and available and supports the voltage rating of the selected 12V
motor and satisfies the current maximum requirements. The L298N motor
driver IC is a dual full bridge driver that is designed to drive
inductive loads such as relays, solenoids, DC and stepping motors by
allowing control of both speed and direction with high voltage and
current up to 46V and 2A per channel under continuous operation and up
to 3A for intermittent operation, featuring built-in diode protection
against back-EMF. As per the product datasheet, the outputs can be
paralleled for higher current output by according to Figure 25,
equivalent parallel pairs are given in for clarity.

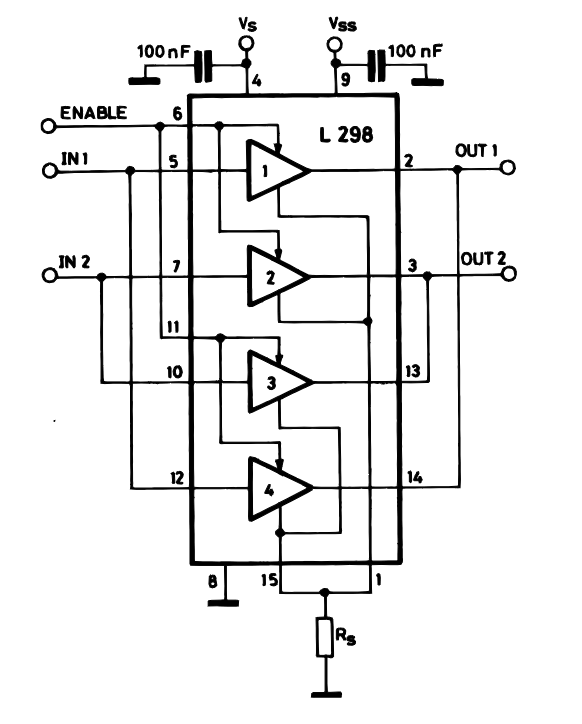
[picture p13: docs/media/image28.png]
A diagram of a circuit Description automatically generated

  -----------------------------------------------------------------------
  **Full Bridge A**                   **Full Bridge B**
  ----------------------------------- -----------------------------------
  IN1                                 IN4

  IN2                                 IN3

  OUT1                                OUT4

  OUT2                                OUT3

  ENA                                 ENB
  -----------------------------------------------------------------------

  : []{#_Toc163515997 .anchor}Figure 7: The retracted (left) and
  deployed (right) CAD renderings of the airbrakes mechanism used by
  ARIS in 2018.

### Flight Sensors

For the flight sensors, the Arduino Pro Nicla Sense ME development board
was chosen due to its comprehensive integration of critical sensors
necessary for monitoring motion and environmental conditions during
flight. This board features various sensors for motion and environment
sensing, all from Bosch known for their high performance and accuracy.
The selection of the Nicla Sense ME allows for a streamlined system
architecture by consolidating multiple sensors onto a single board,
which simplifies the design and enhances the reliability of data
collection for flight dynamics analysis. A summary of the sensors and
their contextual applications is given in Table 10: Arduino Pro Nicla
Sense Motion and Environment Sensors and Contextual Applications.

  -----------------------------------------------------------------------------
  **Sensor Type** **Part**   **Description**                 **Context**
  --------------- ---------- ------------------------------- ------------------
  Accelerometer   BHI260AP   3-axis, part of an integrated   Detecting and
                             sensor hub with AI capabilities analyzing motion
                             for motion detection.           patterns.

  Gyroscope       BHI260AP   3-axis, integrated within       Orientation
                             BHI260AP for orientation and    tracking and
                             motion tracking.                motion correction.

  Pressure        BMP390     Operates between 300 - 1250 hPa Altitude and
                             with high accuracy and low      atmospheric
                             drift for atmospheric           pressure data.
                             measurements.                   

  Magnetometer    BMM150     Measures magnetic fields within Orientation to
                             ±1300μT in X,Y axes and ±2500μT Earth\'s magnetic
                             in Z axis with low noise.       field, used for
                                                             header correction.

  Humidity        BME688     Measures relative humidity as   Unused. Potential
                             part of environmental sensing   future use in
                             capabilities.                   assessing launch
                                                             site conditions.

  Temperature     BME688     Accurate temperature            Unused. Potential
                             measurement as part of the      future use in
                             environmental sensor suite.     assessing launch
                                                             site conditions.

  Gas/VOCs        BME688     Detects a wide range of gases   Unused. Potential
                             including VOCs for air quality  future use in
                             assessment.                     assessing launch
                                                             site conditions.
  -----------------------------------------------------------------------------

  : []{#_Toc163515998 .anchor}Figure 8: Diagrammatic visual of Avionics
  Control Schematic from the University of Ottawa Student Team of
  Aeronautics and Rocketry airbrakes in 2018.

### System Sensors

The System Sensors module encompasses a variety of components designed
to ensure the smooth operation and safety of the mechanism. This
includes the Hall Effect magnetic switches, utilized as end stops to
accurately determine the mechanism\'s extreme positions independently of
the encoder, slider switches for user input, and piezo buzzers for
auditory feedback.

The hall effect sensors were chosen for their simplicity and efficacy as
magnetic switches, acting as critical components for demarcating the
mechanism\'s upper and lower limits. The specific part was selected as
it was on-hand, is 5V compatible, and met space constraints.

The input switches and piezo buzzers are used for preflight programming
if the wireless connection to the MCU fails or is unreliable at the
launch site. It\'s important to note that while piezo buzzers serve as
auditory indicators rather than sensors, they are grouped in this
section for organizational clarity. Auditory indication was selected
over visual indication such as a light due to the difficulty in
predicting where it will be visible post-integration with the rocket.
The piezo buzzers are differentiated by their frequencies to convey
distinct types of feedback: a 2.5 kHz buzzer emits a lower-pitched, less
intrusive sound for confirming actions, while a 4 kHz buzzer produces a
higher-pitched tone designed to capture attention for alerts and
warnings. The chosen buzzers are 5V compatible and have a low profile to
accommodate the spatial constraints. The right-angle mounting design of
the selected input switches facilitates easy access from outside the
rocket, allowing for pre-flight programming through four possible binary
input combinations.

### Microcontroller

At the heart of the system is the Arduino Portenta H7, chosen for its
dual-core architecture combining a high-performance ARM Cortex-M7 and an
energy-efficient Cortex-M4 as part of the STM32H747XI. This enables the
parallel execution of computationally intensive flight computer
algorithms alongside the real-time mechanism control tasks. The
Cortex-M7 core runs at 480 MHz, while the Cortex-M4 core operates at 240
MHz, providing a powerful platform for multitasking. Additionally, the
board is equipped with significant memory resources, including SRAM and
flash memory, to support complex applications and data storage
requirements of this mission critical system.

Ease of programming and futureproofing were a significant factor in this
selection due to board\'s compatibility with high-level Arduino
sketches, allowing for quick development cycles and straightforward
modifications by subsequent teams. Its direct compatibility with the
Nicla Sense ME sensor board facilitates seamless integration, making the
Arduino Portenta H7 an optimal choice for managing the demanding
requirements of both the flight computer and mechanism controller,
leveraging its substantial processing power and versatile development
environment for efficient system performance.

### Power Supply

The power supply for the project relies on Lithium-ion (Li-ion)
batteries, selected for their high energy density and efficiency. The
choice of Li-ion batteries was heavily influenced by competition rules
that explicitly ban the use of Lithium Polymer (LiPo) batteries \[4\]
and our research showed that this is a common alternative used in the
SAC competition. In selection of the battery cells the capacity, max
discharge rate, and voltage requirements were considered. The power
consumption ratings for each of the relevant components is given in
Table 11.

+----------------------+-----------------------+-----------------------+
| **Component**        | **Electrical Power**  | **Details**           |
+======================+=======================+=======================+
| Portenta H7          | 2.6 mA @ 3.7V         | Current consumption   |
|                      |                       | in busy loop (@5V)    |
|                      |                       | \[max with on board   |
|                      |                       | LEDs off\].           |
+----------------------+-----------------------+-----------------------+
| Nicla Sense ME       | 2.5 mA @ 3.7V         | Power consumption     |
|                      |                       | advertising with      |
|                      |                       | sensor polling at 1Hz |
|                      |                       | \[max consumption     |
|                      |                       | state\].              |
+----------------------+-----------------------+-----------------------+
| L298N Motor Driver   | 4 mA @ 12V            | Quiescent supply &    |
| (V~EN~=L)            |                       | VSS current of        |
|                      | 6mA @ 5V              | inactive driver \[max |
|                      |                       | value of range        |
|                      |                       | taken\].              |
+----------------------+-----------------------+-----------------------+
| L298N Motor Driver   | 22 mA @ 12V           | Quiescent supply &    |
| (V~EN~=H)            |                       | VSS current of active |
|                      | 36 mA @ 12V           | driver \[max value of |
|                      |                       | range taken\].        |
+----------------------+-----------------------+-----------------------+
| Brushed DC Motor     | 5000 mA @ 12V         | Stall current of the  |
|                      |                       | selected motor.       |
+----------------------+-----------------------+-----------------------+
| Hall Effect Sensor   | 6.9 mA @ 5V           | Supply current of the |
|                      |                       | IC.                   |
+----------------------+-----------------------+-----------------------+

: []{#_Toc163515999 .anchor}Figure 9: Pancake Airbrakes.

To calculate the required capacity, the 20-hour required standby time
given in ER-003 and an active motor time of 10 seconds (approximately a
FOS of double the predicted motor action time. This yields a total
required capacity of approximately 400 mAh, the calculations are broken
down in Table 12. The datasheet for the Arduino Portenta recommends a
greater minimum of 700 mAh for battery powered use and this will hence
be used as the single cell minimum herein.

  ----------------------------------------------------------------------------------
  **Phase**    **Component**       **Current   **Voltage   **Active   **Energy
                                   (mA)**      (V)**       Time**     Required
                                                                      (mAh)**
  ------------ ------------------- ----------- ----------- ---------- --------------
  Standby      Portenta H7         2.6         3.7         20h        52

               Nicla Sense ME      2.5         3.7         20h        50

               L298N Motor Driver  6           5           20h        120

               Hall Effect Sensor  6.9         5           20h        138

  Standby                                                             360
  Subtotal                                                            

  Active       Brushed DC Motor    5000        12          20s        27.78

               L298N Motor Driver  36          12          20s        0.2
               (Active)                                               

  Active                                                              27.98
  Subtotal                                                            

  *Total                                                              387.98
  Required                                                            
  Energy*                                                             
  ----------------------------------------------------------------------------------

  : []{#_Toc163516000 .anchor}Figure 10: Flap Airbrakes.

The MCU board is supplied with by a single 3.7V cell which the onboard
regulator regulates to 5V to power the 5V components. The DC motor is
rated at 12V therefore 3 cells are required to reach the required
potential which results in a nominal 11.1V (within 10%). As the cells
will be wired in a 3 series (3S) configuration each must independently
be capable of supplying the maximum current of the motor, that is 5000
mA which sets the required minimum discharge current.

This gives a selection criterion of three cells rated at least 700 mAh
each with a minimum discharge rate of 5000 mA. The Panasonic NCR18650GA
3450mAh 10A Battery was chosen for this application as it meets and
exceeds these required specifications while remaining well within
budget. It\'s important to note that most modern lithium-ion cells, even
those that are more affordably priced, meet or exceed the required
specifications for this project making the exact product selection
rather arbitrary. Therefore, the specific selection of the product was
primarily driven by the reputable brand name, price point, and supplier
accessibility. The power to the microcontroller uses the same model of
low-power switch as for the user input and the power switch to enable
power to the motor circuit is a power switched rated up to 6A.

### Development: Full Bridge MOSFET Motor Driver Circuit

The development of a MOSFET full-bridge motor driver circuit was
undertaken. This part is presented as-is and under development which
still requires further validation and verification. Herein, this motor
driver will be referred to as the discrete motor driver. The schematic
for the Production Prototype circuit is given in Figure 26 which
incorporates the discrete motor driver shown in Figure 27. The discrete
motor driver is based on the Allegro A4957 Full Bridge MOSFET Driver
which drives four Nexperia PSMN1R0-30YLC 30V N-Channel MOSFET Power SO8
package. The circuit layout and calculation of passive components
follows closely from the manufacturer datasheet application notes for
the A4957 driver chip. This development was undertaken as it offered the
following advantages it provides over an integrated component such as
the L298N.

Firstly, the discrete motor driver configuration exhibits higher
efficiency due to the A4957 and MOSFETs\' lower on-resistance,
minimizing power losses as heat. Secondly, this setup improves heat
dissipation capabilities as MOSFETs can efficiently spread-out heat over
a larger area compared to integrated circuits; this allows the system to
manage higher currents with less overheating, reducing the reliance on
extensive heat sinking measures that are undesirable in
space-constrained applications such as the present. Additionally, the
use of discrete components results in a more compact and lightweight
solution, again crucial for such applications where space and weight
constraints are important. The performance of motor control is also
enhanced, with better speed and torque management due to the efficient
handling of higher currents and faster switching capabilities of the
MOSFETs. Moreover, this design approach offers greater flexibility,
enabling customization to meet specific requirements more effectively.
Lastly, the discrete motor driver can handle higher voltage and current
levels than the L298N, broadening the range of compatible motors if
future iterations require upsizing of the motor.

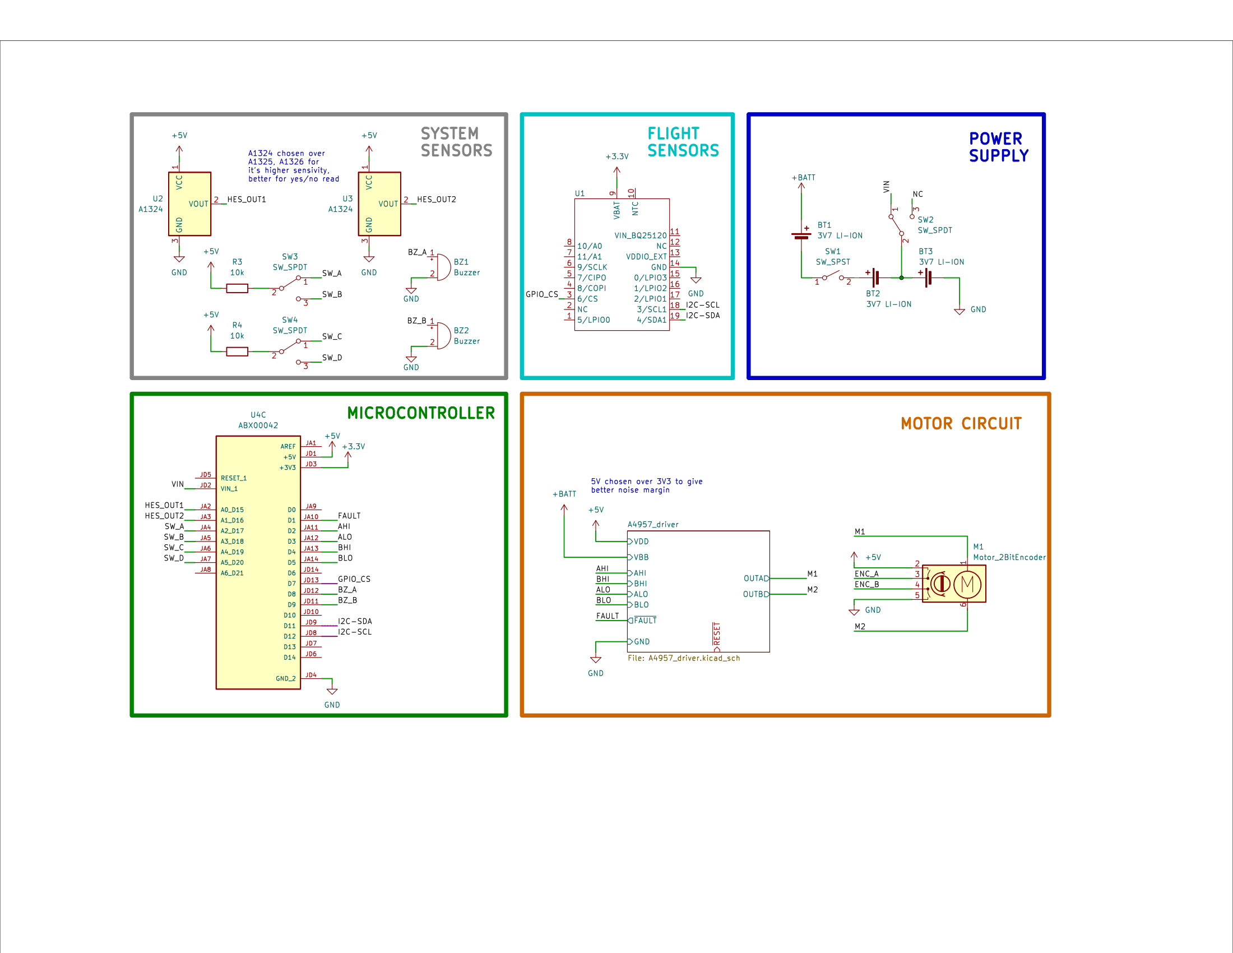
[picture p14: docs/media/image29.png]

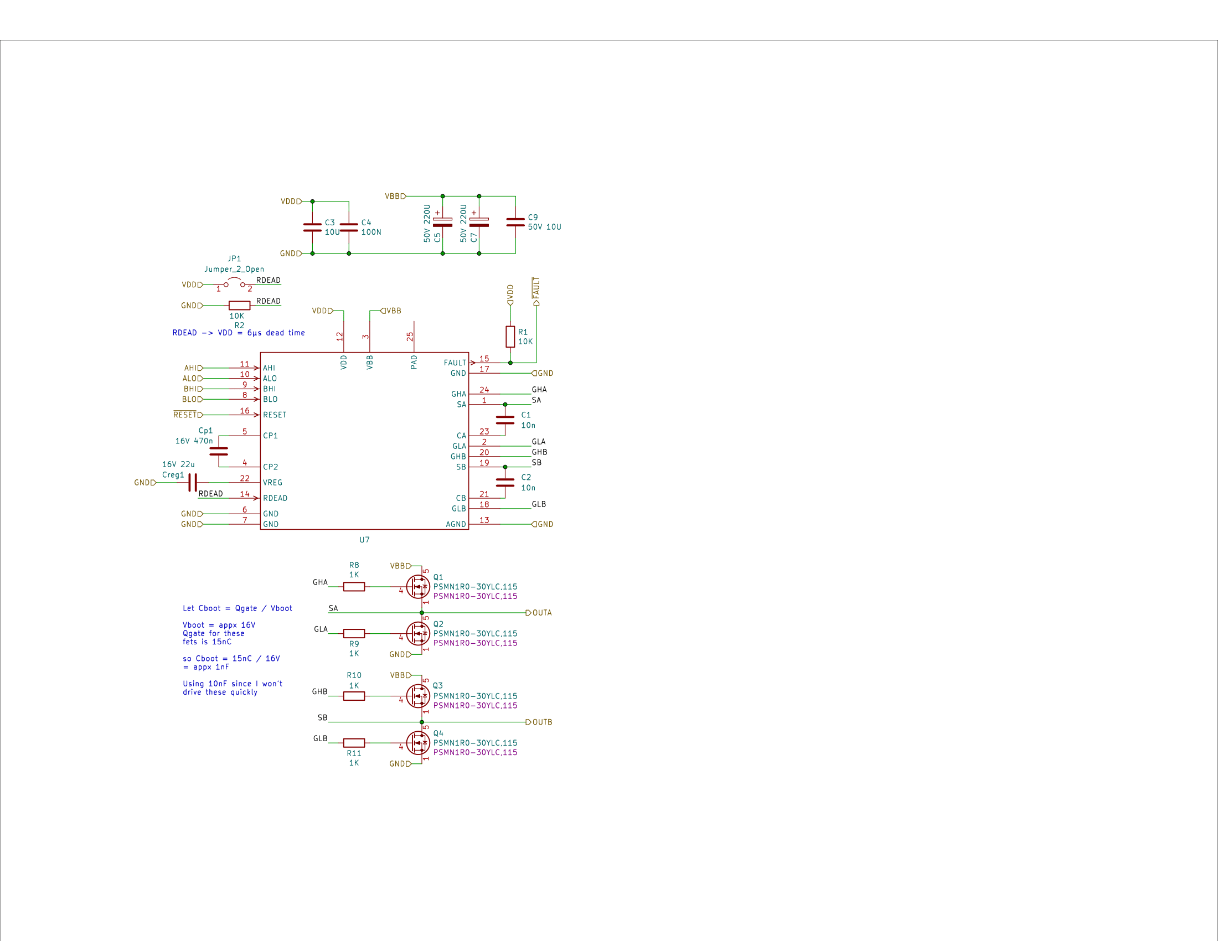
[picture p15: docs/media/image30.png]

### Development: Printed Circuit Board 

The development of a printed circuit board to correspond to the PP
circuit presented above is here presented as-is and under development as
it still requires further validation and verification. The printed
circuit board layout in the editor is displayed in []{.mark}Figure 28.
The discrete motor driver section aligns with the specific routing
patterns and fill plane placement outlined by the manufacturer to reduce
noise, aid thermal management, and optimize layout efficiency.

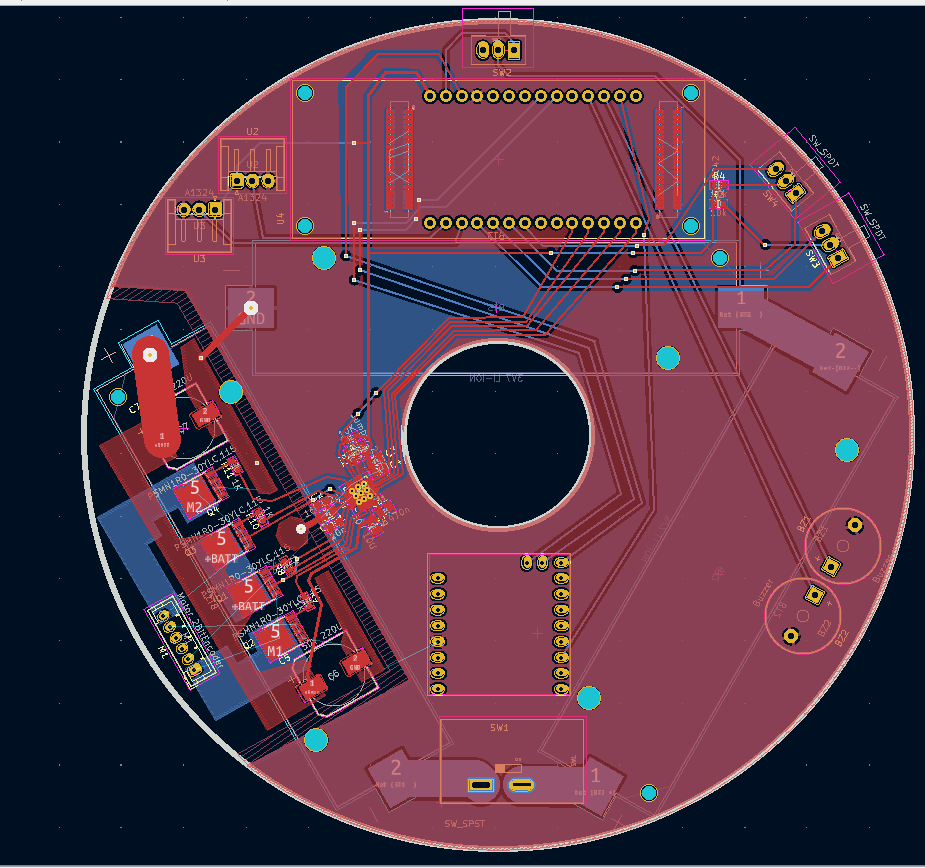
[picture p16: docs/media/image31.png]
A circular object with a hole in the middle Description automatically generated

## Software Design

The overall software design consists of three distinct programs running
in parallel: 1) the flight computer, 2) the actuation controller, and 3)
the sensor client application. The flowchart diagram showing the core

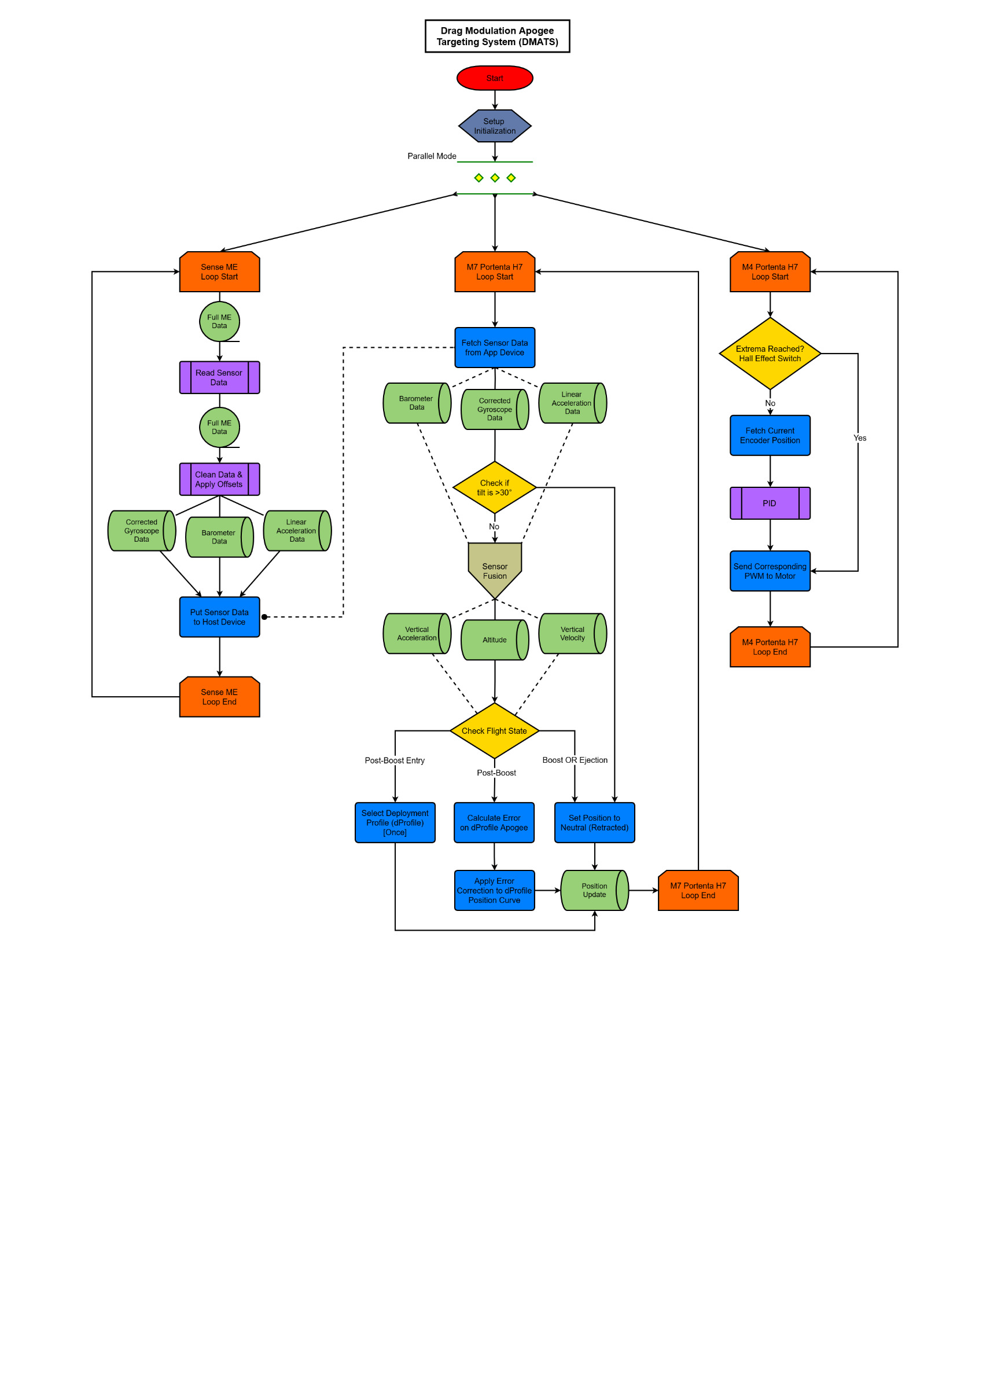
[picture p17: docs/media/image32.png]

### Flight Computer

The flight computer software serves to track the flight of the rocket in
order to inform the actuator controller of its required action to
achieve the desired drag modulation to reach apogee. The flight computer
is a customized version of the HPR-Rocket-Flight-Computer found on
GitHub, created by a registered rocketeer \[26\]. The core of the
program has been developed, however still requires significant
development and testing before flight due to the extensive size and
complexity of the program which contains nearly 10,000 lines of code. An
example of the main loop for the program is included in Appendix III for
brevity and due to the incomplete nature of the entire program. An
important aspect of the software design is the usage of strict data
structures for transporting sensor data and system events in an
organized and structured manner. All relevant program data is
initialized and continuously updated to non-volatile memory of the MCU
such that in the event of a controller reset, the previous state can be
quickly recovered through the rapid recovery routine.

The estimation of the rocket's real-time altitude and vertical motion is
achieved using a two-step Kalman/Complementary filter. A paper by Jung
Keun Lee in 2016 outlines the algorithm which was subsequently
translated into English and implemented as an Arduino library,
AltitudeEstimation \[27\]. The two-step Kalman/Complementary filter for
estimating vertical position with an IMU-Barometer system combines the
high-frequency, noisy acceleration data from the Inertial Measurement
Unit (IMU) with the more stable but lower-frequency altitude
measurements from the barometer. Initially, the Kalman Filter integrates
both data sources to correct the IMU's drift by weighing their
reliability, providing an optimized estimate of vertical position.
Subsequently, a complementary filter refines this estimate by balancing
the IMU's short-term accuracy against the barometer's long-term
stability, effectively minimizing temporary errors and response lag.
This dual-filter approach thus achieves accurate vertical positioning by
harnessing the strengths of both sensors, crucial for applications
requiring precise altitude control \[28\].

Once the flight computer algorithm detects that the rocket has exited
the boost phase and has entered the coast phase, it takes the current
state (i.e. current velocity and altitude) and compares it against a
lookup table generated from simulations. It selects the path from the
lookup table that most closely matches and sends the corresponding
deployment angle to the actuation controller running on the other core.

### Actuation Controller

The actuation controller consists of a closed feedback loop between the
desired position and the current position returned by the encoder. To
achieve this, a library was developed based on a legacy library \[29\]
inspired by AccelStepper library by Adafruit \[30\] and uses both the
Encoder library \[31\] and PID library \[32\] available in the Arduino
library manager. The header and main C++ file for the library can be
found in Appendices IV & V. Additional examples and scripts were created
to test the feedback of the encoder, tune the PID action, and configure
preset distances \[33\].

### Sense Client App

The client application that runs on the Nicla Sense ME is an unaltered
version provided by the manufacturer to set the device to act as a
client device and is given in Appendix VI.

## References

\[16\] J. Bochnia, M. Blasiak, and T. Kozior, "A Comparative Study of
the Mechanical Properties of FDM 3D Prints Made of PLA and Carbon
Fiber-Reinforced PLA for Thin-Walled Applications," *Materials (Basel)*,
vol. 14, no. 22, p. 7062, Nov. 2021, doi: 10.3390/ma14227062.

\[17\] J. A. Travieso-Rodriguez, R. Jerez-Mesa, J. Llumà, O.
Traver-Ramos, G. Gomez-Gras, and J. J. Roa Rovira, "Mechanical
Properties of 3D-Printing Polylactic Acid Parts subjected to Bending
Stress and Fatigue Testing," *Materials (Basel)*, vol. 12, no. 23, p.
3859, Nov. 2019, doi: 10.3390/ma12233859.

\[18\] A. Kholil, E. Asyaefudin, N. Pinto, and S. Syaripuddin,
"Compression Strength Characteristics of ABS and PLA Materials Affected
by Layer Thickness on FDM," *J. Phys.: Conf. Ser.*, vol. 2377, no. 1, p.
012008, Nov. 2022, doi: 10.1088/1742-6596/2377/1/012008.

\[19\] "Polymers \| Free Full-Text \| Strength of PLA Components
Fabricated with Fused Deposition Technology Using a Desktop 3D Printer
as a Function of Geometrical Parameters of the Process." Accessed: Apr.
07, 2024. \[Online\]. Available: https://www.mdpi.com/2073-4360/10/3/313

\[20\] E. A. Syaefudin, A. Kholil, M. Hakim, D. A. Wulandari, Riyadi,
and E. Murtinugraha, "The effect of orientation on tensile strength 3D
printing with ABS and PLA materials," *J. Phys.: Conf. Ser.*, vol. 2596,
no. 1, p. 012002, Sep. 2023, doi: 10.1088/1742-6596/2596/1/012002.

\[21\] "Zonal Two Equation k-w Turbulence Models For Aerodynamic Flows
\| Fluid Dynamics and Co-located Conferences." Accessed: Apr. 08, 2024.
\[Online\]. Available: https://arc.aiaa.org/doi/10.2514/6.1993-2906

\[22\]
"Team_127_Project_Technical_Report_to_the_2023_Spaceport_America_Cup.pdf -
Google Drive." Accessed: Apr. 08, 2024. \[Online\]. Available:
https://drive.google.com/file/d/18ZheeMO8H3UuRlllgGhdWLznT8SM7l4D/view

\[23\] "7450M2505-P Data (RockSim) • ThrustCurve." Accessed: Apr. 08,
2024. \[Online\]. Available:
https://www.thrustcurve.org/simfiles/5f4294d20002e900000005a0/

\[24\] R. Products, I. \| 645 E. E. Ave, Kirkwood, I. A. rights reserved
\|Lead Time, and I. I. \|Return Policy, "Acme Lead Screws & Nuts -
Engineering Data \| Roton Products Inc.," Roton Products, Inc. Accessed:
Jan. 19, 2024. \[Online\]. Available:
https://www.roton.com/products/acme-lead-screws-nuts/engineering-data/

\[25\] STElectronics, "Dual full-bridge driver Datasheet DS0218 - Rev
5." ST Electronics, Oct. 2023. \[Online\]. Available:
https://www.st.com/resource/en/datasheet/l298.pdf

\[26\] SparkyVT, "SparkyVT/HPR-Rocket-Flight-Computer." Apr. 06, 2024.
Accessed: Apr. 08, 2024. \[Online\]. Available:
https://github.com/SparkyVT/HPR-Rocket-Flight-Computer

\[27\] "juangallostra/AltitudeEstimation: A two-step
Kalman/Complementary filter for Estimation of Vertical Position using an
IMU-Barometer sytem." Accessed: Apr. 08, 2024. \[Online\]. Available:
https://github.com/juangallostra/AltitudeEstimation

\[28\] S. D. Levy, "simondlevy/TwoStepFilter." Apr. 04, 2024. Accessed:
Apr. 08, 2024. \[Online\]. Available:
https://github.com/simondlevy/TwoStepFilter

\[29\] "julester23/DCMotorServo: Arduino Library for controlling DC
motors with rotary encoders." Accessed: Apr. 08, 2024. \[Online\].
Available: https://github.com/julester23/DCMotorServo

\[30\] "adafruit/AccelStepper." Adafruit Industries, Mar. 08, 2024.
Accessed: Apr. 08, 2024. \[Online\]. Available:
https://github.com/adafruit/AccelStepper

\[31\] P. Stoffregen, "PaulStoffregen/Encoder." Mar. 30, 2024. Accessed:
Apr. 08, 2024. \[Online\]. Available:
https://github.com/PaulStoffregen/Encoder

\[32\] br3ttb, "br3ttb/Arduino-PID-Library." Apr. 08, 2024. Accessed:
Apr. 08, 2024. \[Online\]. Available:
https://github.com/br3ttb/Arduino-PID-Library

\[33\] "CameronBrooks11/DCMotorServo: An Arduino Library for controlling
DC motors with rotary encoders." Accessed: Apr. 08, 2024. \[Online\].
Available: https://github.com/CameronBrooks11/DCMotorServo

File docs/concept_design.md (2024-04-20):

# Conceptual Design
Consists of the generation and evaluation of proposed designs.

## Mechanical Concept Generation

After conducting the study on prior art and emerging technologies, the
concept generation process began. Through structured brainstorming and
extensive research, four distinct concepts for the airbrake system's
mechanical design were developed.

### Pancake 

Pancake-style airbrakes are characterized by radially deploying flaps
that can be controlled by a servo or stepper motor. This design offers a
compact solution that incorporates flaps that are initially flush with
the rocket's airframe and then extend outwards, perpendicular to the
airflow. These extended flaps generate drag, thus reducing the airspeed
of the rocket. The pancake airbrakes can be driven by a slider crank
mechanism or geared together. The flaps are typically made of aluminum,
ensuring robustness while minimizing weight. Figure 9 depicts an example
of the pancake style airbrakes used in École Polytechnique Fédérale de
Lausanne's rocket design that competed in the Spaceport America Cup in
2018. 

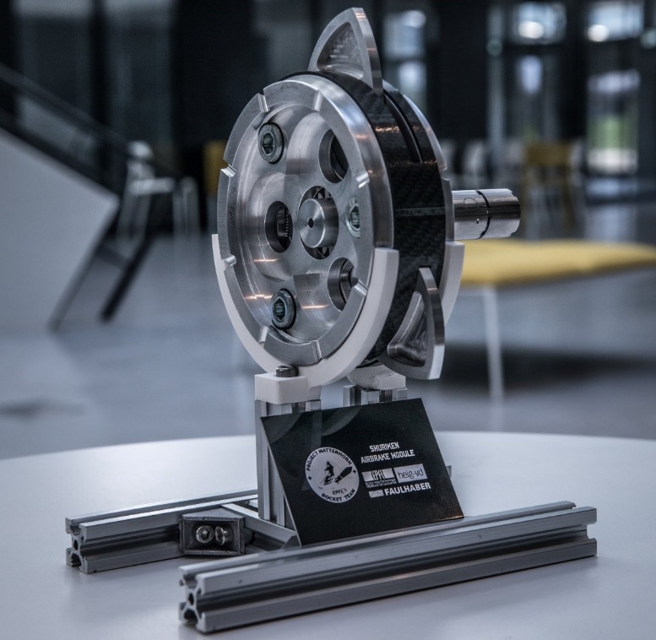
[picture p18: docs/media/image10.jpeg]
No photo description available.


### Flaps 

Flaps-style airbrakes are a commonly used design in model rocketry that
offer precise apogee control. This design consists of hinged panels or
flaps that are initially flush with the rocket's airframe and then
deploy to induce drag. The flaps can be controlled remotely or be
programmed to actuate at specific speeds or altitudes. For deployment, a
servo or stepper motor can move a single platform along a lead screw to
actuate rods up and down. As the lead screw is actuated, the hinges move
out of the airframe to deploy the flaps. The flaps can be made of either
aluminum or carbon fiber. Figure 10 provides an example of a flap-style
airbrake system.

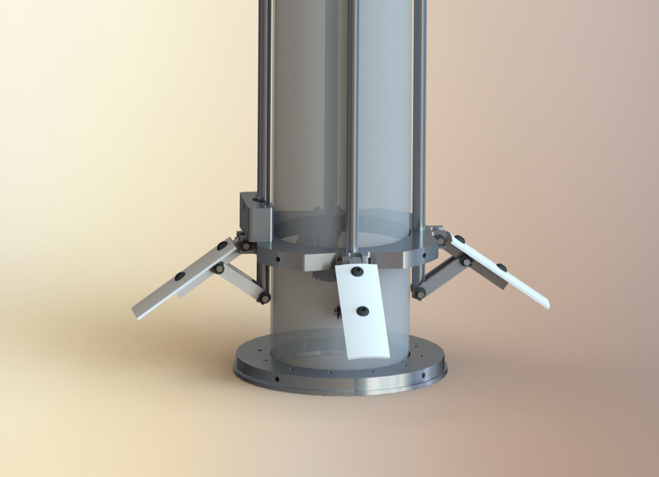
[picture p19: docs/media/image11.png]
A metal cylinder with metal rods Description automatically generated with medium confidence


### Doppler Hole

The Doppler hole style of airbrakes is a novel, never tested concept
where holes are strategically cut into the rocket structure to generate
drag. These openings allow air to flow into the rocket body and increase
the rocket's drag. As the number of holes increases, the more drag is
produced. Unlike the other generated concepts, this style of airbrake
operates passively, and cannot be adjusted, negating the need for a
control system. Critical factors involved in this design are the size,
shape, and placement of the holes. Figure 11 depicts a conceptual model
of the doppler hole airbrake system.

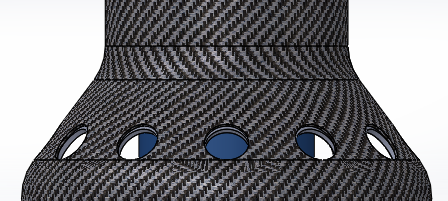
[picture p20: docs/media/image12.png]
A close up of a black and white object Description automatically generated


### Origami Flashers

The origami flasher airbrakes are an adaptation of the pancake style
airbrakes. As the name suggests, this design is inspired by the Japanese
art of paper folding. In this concept, the intricate folding pattern is
deployed and creates a geometric surface that generates drag. The
controlled unfolding of the pattern is a critical aspect of the design
and can be achieved using mechanical actuators, spring, or pyrotechnics.
The geometric pattern must be carefully optimized to achieve the desired
aerodynamic performance that meets the project requirements. An example
of the origami flasher concept is provided in Figure 12.

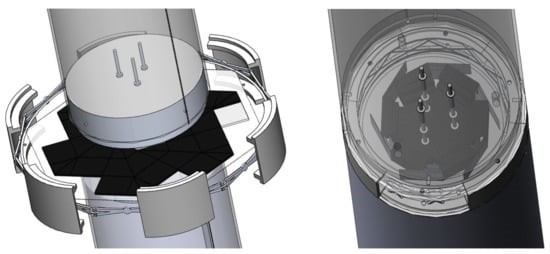
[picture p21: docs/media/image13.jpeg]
Jcs 05 00147 g014 550


## Mechanical Concept Evaluation 

After the concept generation phase, the next step in the design process
was to evaluate each concept to determine which approach will best meet
the project objectives and requirements. Comprehensive criteria were
then developed to assess each concept. The specific criteria included:

1.  Precision Apogee Targeting

2.  Safety

3.  Technology Readiness Level (TRL)

4.  Electrical Simplicity

5.  Mechanical Simplicity

6.  Ease to Simulate

7.  Simulation Accuracy

8.  Cost

9.  Ease of Manufacture

10. Mass

11. Durability

12. Redundancy

13. Length

14. Repairability

15. Reliable Deployment

16. Auto-Closing

Using the above criteria, a House of Quality (HOQ) and Pugh Matrix were
constructed to compare each concept. The HOQ and Pugh Matrix can be
found in Appendix I. In both methods, the concept that scored the
highest was the flap style airbrakes. The flap style airbrakes system
triumphed compared to other designs for its high durability, redundancy,
ease of manufacturability, and easy repairability. The flap style design
also has flight heritage and a high TRL, unlike the Doppler hole and
origami flashers concepts, which have both never been flown before.

At the concept selection phase, the airbrakes design consisted of four
flaps. Four flaps in the design meant that a critical safety feature
could be implemented such that the flaps retract in a neutral state if
one of them fails. This feature was considered incredibly important and
was a primary factor for choosing the flaps style airbrakes. However, in
January, the rocketry team shifted the rocket design to have three fins
instead of four. The number of flaps must match the number of fins to
ensure adequate stability of the rocket. Consequently, the design change
to three flaps meant the auto-retracting feature could no longer be
implemented. Instead, the software must include a feature to detect the
failure of a single flap and cause the airbrakes to retract.

The areas in which the flaps style design scored lower than the other
concepts were length and mass. However, the system requirements defined
a large range for these criteria that the airbrakes design can easily
meet. Careful consideration for material and design choices would also
make the flap style airbrakes successfully meet these requirements.

## Electrical Concept Generation

After conducting the study on prior art and emerging technologies, the
concept generation process began. Through structured brainstorming and
extensive research, four distinct concepts for the airbrake system's
mechanical design were developed.

### Commercial-off-the-Shelf (COTS) Flight Computer

This idea centers on employing a commercial flight computer to integrate
into the airbrakes system. This flight computer would process crucial
flight data such as altitude and velocity to make decisions on the fly
regarding the deployment of airbrakes. Communication between the flight
computer and the actuation mechanism of the airbrakes could be achieved
through I2C or serial connections linked to a microcontroller unit (MCU)
that would directly manage the actuator. There would also be the
possibility of programming the flight computer's outputs to take control
of the actuation mechanism on its own. The advantage of this approach
lies in its potential to slash development time by leveraging
pre-constructed components, coupled with the high reliability that
commercial flight computers are known for. However, this method might
fall short in terms of customization capabilities, and would likely be
more costly than bespoke solutions, and introduces a dependency on
external suppliers for technical support.

### Microcontroller Unit (MCU)

Opting for an MCU as the backbone of the electrical scheme affords the
liberty to create a tailored flight program to monitor and control the
airbrakes mechanism. This approach requires programming the MCU to
interpret inputs from various sensors and execute airbrake deployment
based on established criteria. Selection criteria for the MCU would
hinge on its processing prowess, I/O capabilities, and sensor and
actuator compatibility. This path provides a high level of
customization, allowing for potentially better alignment with specific
project requirements and direct oversight over system integration.
Furthermore, MCUs are more economically feasible compared to
off-the-shelf alternatives. Nevertheless, it comes with its share of
challenges, including a lengthy development and testing phase of the
complete program, and a heightened risk of encountering bugs and
reliability issues without comprehensive testing.

### Field-Programmable Gate Array (FGPA)

Integrating an FPGA into the design allows for an advanced,
customizable, and performance-tuned control system. FPGAs are renowned
for their programmability to execute specific control logic and
processing tasks at remarkable speeds, which is ideal for real-time
applications such as high-speed active control. This option involves
crafting the logic and control algorithms for FPGA implementation. The
strengths of employing an FPGA include unparalleled real-time processing
and control performance, immense design flexibility and
reconfigurability, and the efficient handling of complex algorithms and
control logic. However, FPGAs come with a steeper learning curve and
greater complexity in programming compared to MCUs, generally higher
initial costs for development tools and components, and necessitate
specialized expertise for effective deployment.

## Electrical Concept Evaluation

After an extensive evaluation of the various electrical concepts for the
airbrakes system, the team decided to proceed with a Microcontroller
Unit (MCU)-based architecture. This decision aligns with our project's
specific needs, constraints, and goals, emphasizing the balance between
customization, cost-effectiveness, and manageable development timelines.

The choice of an MCU was driven by its superior flexibility in
customization. This allows our team to develop a flight computer and
actuator control programs tailored to our system, a level of specificity
that commercial-off-the-shelf (COTS) solutions cannot match. The ability
to finely tune and optimize the system is paramount, especially in
achieving the precision necessary for airbrake deployment to hit the
target apogee with minimal deviation. This customization capability is
crucial, even more so because the Western Engineering Rocketry Team is
moving towards developing their own Student Research and Developed
(SRAD) flight computers for future avionics applications. Adopting an
MCU for this project represents a strategic step towards building
in-house expertise in custom flight computer development, setting a
foundational knowledge base for future projects.

From a financial perspective, an MCU-based solution presents a more
economical option compared to both COTS flight computers and the more
advanced FPGA alternatives. The lower cost of MCUs, coupled with their
widespread availability and the extensive support materials available,
renders this path particularly attractive for a student project with
budgetary constraints.

The development timeframe was another critical factor in the decision to
choose an MCU. Despite the high performance and real-time processing
capabilities of FPGAs, they require specialized programming skills and
come with a steeper learning curve. Given the team\'s relative
proficiency with MCU programming and the abundant resources and
community support available for various MCU platforms, there is an
anticipation of a smoother and quicker development and testing phase
with an MCU, ensuring project timelines are met efficiently. Moreover,
the broad support for MCUs from both manufacturers and a global
community of developers offers an invaluable resource. 

However, selecting an MCU over a COTS flight computer comes with its own
set of implications that the team is cognizant of. While there is a gain
in customization and cost, the increased responsibility on the
development team must be acknowledged to ensure the reliability and
robustness of our custom solution. Developing the flight software
demands a comprehensive understanding of the system's requirements and a
thorough approach to testing and validation. Furthermore, this choice
necessitates a proactive approach to both the overall system design as
well as the subsequent documentation and knowledge transfer to ensure
that future teams can build upon the capstone team's work.

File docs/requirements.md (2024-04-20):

# Design Requirements and Constraints

## Preamble

The following is an outline of the most important design requirements
for the airbrakes system, as needed to understand the contents of the
final report. Other requirements that did not have a major effect on the
contents of this report may be found in Rev 1 of the Project
Requirements document.

The design requirements were generated primarily from two sources:
consultation with the rocketry team to determine the specifications of
an airbrakes system that could be integrated into this year's rocket,
and competition requirements, principally those found in the DTEG \[2\],
the competition Rules and Requirements Document \[4\], and the Range
Standard Operating Procedures \[5\].

The requirements laid out in the following sections fall into two
categories:

1.  "Shall" requirements are requirements that must be met for the
    system to conform to this specification.

2.  "Should" requirements are recommendations which would be nice to
    have and which the team should endeavour to achieve if it is
    feasible and does not come at the expense of failing to meet any
    "shall" requirement(s).

## Functional Requirements

The functional requirements define the features and/or functions of the
airbrake system that must be implemented to achieve the desired
outcomes. Table 1 provides a summary of the most important functional
requirements, along with the rationale for each.
| **Requirement ID** | **Requirement** | **Rationale** |
|---|---|---|
| FR-002 | The system shall induce the correct amount of drag such that the rocket achieves its 10,000 ft target apogee to within +/- 200 ft. | The purpose of the airbrakes system is to enable the rocket to have a final apogee of as close as possible to 10,000 ft to maximize the team's flight score as laid out in section 2.7.1.4 of the SAC Rules & Requirements Document [4]. This score given for precise apogee targeting is 35% of the total points that a team can earn during the competition. +/- 200 ft is an achievable goal for most teams using airbrakes at SAC. Being 200 ft off-target would result in the rocketry team achieving 327 out of 350 possible points for final apogee, as per section 2.7.1.4 of the SAC Rules & Requirements Document [4]. |
| FR-003 | The system shall survive exposure to 13.58gs of force when in its stowed configuration. | As determined by flight simulations (OpenRocket, RocketPy, custom flight simulator). See Section 11.4.5 for the determination of the value. |
| FR-004 | The system shall survive exposure to the aerodynamic loading expected during max q: 48.7 kPa. | As determined by flight simulations (OpenRocket, RocketPy, custom flight simulator). See Section 11.4.5 for the determination of the value. Note that the flaps will never be deployed at max-q, because as per section 7.4 in SAC Design, Test, & Evaluation Guide, that is when they may begin to deploy [2]. |
| FR-006 | The system shall default to a neutral state if any of the following occur: - The controller sends an abort signal. - Primary system power is lost. - The rocket's attitude exceeds 30° from its launch elevation. | A neutral state is defined as one which does not apply any moments to the rocket.|
| FR-007 | The system shall remain in a neutral state until at least one of the following have occurred: - The rocket's boost phase has ended (i.e., all propulsive stages have ceased producing thrust), - The launch vehicle has crossed the point of maximum aerodynamic pressure (max Q) in its trajectory, - Or the launch vehicle has reached an altitude of 6,500 ft (2,000 m) AGL. | A neutral state is defined as one which does not apply any moments to the rocket. Competition requirement as per section 7.4 in SAC Design, Test, & Evaluation Guide [2]. The rocket has virtually no chance of clearing 20,000 ft before either of the first two conditions are met. In addition, with a single stage rocket of the order of magnitude of the WE Rocketry Team's previous rocket in the 10,000 ft category, the first two conditions will be met within a second of each other (as determined by the flight simulations detailed in Section 11.4). Therefore, the airbrakes can easily target a second or two after engine cut-off for a release of its mechanical locking system. |

## Physical Requirements

The physical requirements define the physical attributes, including
dimensions and material requirements, of the airbrake system. Table 2
provides a summary of the most important physical requirements for the
system, along with the rationale for each.
| **Requirement ID** | **Requirement** | **Rationale** |
|---|---|---|
| PR-001 | The system shall have a 5.5'' diameter when in its neutral/stowed state. | The rocket will have a 5.5'' diameter. The flaps cannot stick out of the airframe when stowed, and the transfer of force along the longitudinal axis of the rocket would be less safe if the outer diameter of the structure was smaller over the airbrakes section. |
| PR-002 | The system shall have a mass of less than 4 kg. | 4 kg is the maximum mass that WE Rocketry is willing to allocate to the airbrakes system. |
| PR-003 | The system shall be less than 30 cm long. | The system must both reasonably fit within a body tube section along with other components, and not elongate the rocket so much as to undermine its stability. 30 cm is the length allotted by WE Rocketry to the airbrakes system, and is consistent with the length of other airbrakes systems observed at competition. |

## Electrical Requirements

The electrical requirements refer to the electrical specifications that
the airbrake system must comply with to achieve the desired outcomes.
Table 3 provides a summary of the most important electrical requirements
for the system, along with the rationale for each.
| **Requirement ID** | **Requirement Description** | **Rationale** |
|---|---|---|
| ER-002 | The system shall have safety-critical wiring with proper cable management for airbrake deployment. | Wiring associated with airbrake deployment is considered safety-critical since it can affect the rocket trajectory or stability as per Sections 6.11 & 6.12 of the SAC Design, Test, & Evaluation Guide [2]. |
| ER-003 | The system shall have a dedicated power supply separate from the rocket's main avionics. | To ensure that the airbrake system remains operational even if the main avionics fail.  |
| ER-004 | The battery shall provide a minimum of 20 hours of continuous operation and support the electrical demands of the actuator. | A 12 V battery is chosen to directly power the motor for the airbrakes, which generally require higher voltages for optimal performance.  |
| ER-005 | The system shall have real-time data acquisition from accelerometers and pressure sensors. | Real-time data is essential for adaptive control of airbrakes during flight.|
| ER-006 | The electrical subsystem shall incorporate fail-safe logic that mechanically locks the airbrakes in a neutral state upon loss of electrical power. | To meet FR-006 and ensure safety in case of system failure. |
| ER-007 | The electrical subsystem and its components shall be capable of operating in a temperature range of 5°C to 70°C. | To comply with ENR-003 and ensure functionality under harsh and varying environmental conditions.  |

## Programmatic Requirements

The programmatic requirements refer to the specific needs that are
required to meet technological, programmatic, or regulatory demands.
Table 4 provides a summary of the most important programmatic
requirements for the system, along with the rationale for each.

## References
\[2\] "Spaceport America Cup Intercollegiate Rocket Engineering
Competition Design, Test, & Evaluation Guide." The Experimental Sounding
Rocket Association (ESRA), Oct. 24, 2023. Accessed: Apr. 08, 2024.
\[Online\]. Available:
https://www.soundingrocket.org/uploads/9/0/6/4/9064598/2023-sa_cup_dteg_v2.2.9_10-24-23.pdf
\[4\] "Spaceport America Cup Intercollegiate Rocket Engineering
Competition Rules & Requirements Document." The Experimental Sounding
Rocket Association (ESRA), Mar. 04, 2024. Accessed: Apr. 08, 2024.
\[Online\]. Available:
https://www.soundingrocket.org/uploads/9/0/6/4/9064598/sa_cup_irec_rules_and_requirements_document\_-2024_v1.4_20240304.pdf

\[5\] "Spaceport America Cup Range Standard Operating Procedures." The
Experimental Sounding Rocket Association (ESRA), Jun. 15, 2023.
Accessed: Apr. 08, 2024. \[Online\]. Available:
https://www.soundingrocket.org/uploads/9/0/6/4/9064598/sa_cup_irec_range_standard_operating_procedures_2023-a.pdf

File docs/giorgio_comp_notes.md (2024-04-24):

Notes from SAC 2023

## Rocketry Advice from Canterbury and Maryland

### Canterbury's Advice:
- **Static Ports Placement:** Do not position the rocket's static ports directly above the airbrakes.
- **Deployment System:** Utilize a single motor to drive all flaps (either 3 or 4). Partial deployment, such as only 2 flaps deploying, can turn a rocket into a ballistic missile.
- **Control System:** PID (Proportional-Integral-Derivative) control works well for airbrake systems; there's no need for more complex solutions.
- **Design For Assembly (DFA):** Consider ease of assembly in the design process.

### Maryland's Advice:
- **Flap Design:** Opting for flaps is safer because, in case of failure, they tend to fail inwards, minimizing risk.
- **System Separation:** It's advisable to keep the airbrake system entirely separate from the avionics bay for simplicity. Consider equipping it with its own barometer and accelerometer.
- **Sensor Readings:** Barometer readings can be affected by flap deployment. This can be corrected through characterization from wind tunnel testing, which tends to be very effective. Alternatively, a well-developed CFD model could also provide accurate predictions.
- **Simulation Considerations:** Include the deployment time of airbrakes in flight simulations, and consider how angle of attack might affect induced drag and vertical velocity.

## Terrapin Rocket Team's Rockets at Spaceport America Cup:
- **2022**: [Terrapin Rocket Team - Spaceport America Cup 2022](https://www.terprockets.com/spaceport-america-cup-2022)
- **2023**: [Terrapin Rocket Team - Spaceport America Cup 2023](https://www.terprockets.com/spaceport-america-cup-2023)

## Common Parts and Material Choices:
- **Actuators:** Linear actuators or stepper motors are commonly used.
- **Materials for Blades:** Blades are often made from aluminum or carbon forged materials.
- **Example Specification:** For smaller rockets, such as those with a 3-inch diameter airframe, an LA-T8 6V 1mm/s 50mm 128N linear actuator is suitable.

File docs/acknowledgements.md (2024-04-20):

# Acknowledgements

The capstone team would like to thank the following people for their
support:

Our faculty advisor Dr. John Makaran, for his guidance and mentorship.

The Department of Mechanical and Materials Engineering and the
Department of Electrical and Computer Engineering, for allowing a
cross-discipline capstone team for this project.

The WE Rocketry team, for their collaboration, sponsorship, and support.
The team would like to specifically thank Chief Engineer Jessica Kerr,
the aerostructures team, the propulsion team, and alumnus Niall Bannigan
for their support of the project.

Mesfin Gebreyes for helping the team perform destructive compression
testing in Western's Tensile Testing Laboratory.

Alex Nutting for his assistance in the manufacturing of the lead screw.

The Boundary Layer Wind Tunnel for allowing the team to use the wind
tunnel free of charge, and in particular Darren Garnham for facilitating
and organizing our use of the facility.

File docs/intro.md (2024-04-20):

# Introduction

The Western Engineering Rocketry Team competes annually in the
Intercollegiate Rocket Engineering Competition. For the 2023-2024
iteration, the team aims to improve apogee targeting by integrating an
airbrake system into their rocket designed to reach 10, 000 feet. The
main challenge is engineering an airbrake system that will induce a
controlled amount of drag during the rocket's ascent to closely achieve
the desired apogee. The project encompasses multiple domains, including
mechanical, electrical and software design.  

The project began with concept generation that involved brainstorming
sessions, research, and cross-disciplinary collaboration. Various
concepts, notably flap-style and pancake-style airbrakes, were explored.
After a comprehensive evaluation process, the flap-style airbrake
concept was selected as the most promising for the project. 

The detailed design phase focused on creating a CAD model, engineering
drawings, and material selection for the airbrake components. Iterative
design reviews and feedback ensured the final design met the project
requirements.

Prior to the manufacturing of the functional prototype, extensive
simulations were conducted to validate the design. Finite Element
Analysis and Computational Fluid Dynamics were employed to guide the
design and ensure safety margins would be met.

The mechanical design when manufactured and assembled functioned as
intended and inspired confidence that it will perform well during
flight. A few changes were made to the design during the prototyping
stage as various small problems arose during assembly. The first change
made was the addition of a motor mount to adequately secure the motor to
the top platform and the lead screw. The second change made was to add
platform support members, which served two purposes. First, these
supports guaranteed a fixed distance between the top and bottom
platforms, ensuring that there will be no binding of the lead screw.
Secondarily, it means that the airbrake system can be installed as a
single unit into a coupler tube, vastly simplifying the rocket
installation process.

## Description of Need

The Western Engineering Rocketry Team (WE Rocketry) competes annually at
the Spaceport America Cup, the largest intercollegiate rocketry
competition in the world. For the 2024 competition, the team will be
competing in the 10k feet COTS motor category.

At competition, 35% of a team's score is based on how close their apogee
is to their competition category's target apogee. The most competitive
teams at the competition hit within 100 ft of their apogee target \[1\].
Doing so reliably without the use of an active flight control system is
unfeasible, as minor variations in conditions that are outside of the
team's control (including atmospheric conditions, motor thrust
variability, and the launch rail angle set by Range Safety Officers on
launch day \[2\]) can lead to significant deviations from what can be
simulated, or even achieved in a previous test flight.

The most commonly used form of active control for precision apogee
targeting at competition are airbrakes systems \[3\]. WE Rocketry
intends to integrate an airbrakes system into their rocket for the 2024
Spaceport America Cup to target a 10,000-foot apogee with more precision
than would be possible without an active control system.

##  Report Scope

This report and the other files provided alongside it (part drawings,
the costed BOM, and the project Gantt chart) constitute the final
deliverables of the capstone course, and as such provide a summary of
all the work done on this project up until the due date of the report.
It should be noted at the outset that the airbrakes project does not end
with the conclusion of the capstone course. Further work needs to be
done before the competition in June, and forward-looking remarks for
this project are included in Section 14: Recommendations, Future Design
Directions.

# Problem Definition

The capstone project was undertaken with the objective of creating WE
Rocketry's first airbrakes system to make the team more competitive at
the Spaceport America Cup. An airbrakes system is an electromechanical
assembly that extends outwards from the body of a rocket or aircraft
during flight to induce drag to decelerate the rocket or aircraft. There
are different ways of implement aerobraking on a rocket -- the two most
common of which are flap-style and pancake-style systems, which will be
discussed in more detail in Section 9: State-of-the-Art and Emerging
Technologies and Section 10: Concept Generation and Evaluation -- but
the main principles stay the same regardless of the mechanism (by
extending a control surface into the freestream flow to induce drag).

There are many considerations that must be made when fitting a rocket
with an airbrakes system. Ensuring the rocket's structural integrity and
aerodynamic stability are of paramount importance. The requirements in
the following section are the result of the first phase of the design,
which defined the scope of the problem, as well as the requirements and
constraints for the airbrakes system.

## References
\[1\] "2023 SA Cup," ESRA. Accessed: Apr. 08, 2024. \[Online\].
Available: https://www.soundingrocket.org/2023-sa-cup.html

\[2\] "Spaceport America Cup Intercollegiate Rocket Engineering
Competition Design, Test, & Evaluation Guide." The Experimental Sounding
Rocket Association (ESRA), Oct. 24, 2023. Accessed: Apr. 08, 2024.
\[Online\]. Available:
https://www.soundingrocket.org/uploads/9/0/6/4/9064598/2023-sa_cup_dteg_v2.2.9_10-24-23.pdf

\[3\] "IREC Reports - Google Drive." Accessed: Apr. 08, 2024.
\[Online\]. Available:
https://drive.google.com/drive/folders/14pfiOCJ2Xkqqd72IAzEHdSXjxMHer6_0

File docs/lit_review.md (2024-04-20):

# Literature Review

## Background

### Search Strategies & Terms

Key words terms (KWT)

1. "airbrakes" AND "sounding rocket"
2. "air brakes"
3. "rocket" AND "apogee targeting"
4. "airbrakes" OR "air brakes"
5. "rocket airbrakes"
6. "drag" AND "rocket"
7. "airbrakes" AND "SRAD"
8. "airbrakes" AND "github"
9. "airbrakes" AND "gitlab"

Strategies

1. Searched KWT 1-7 on duckduckgo

### What are Airbrakes?
TODO

### Theoretical Framework
TODO

### Significance and Importance
TODO

### Current State of the Art

#### Swiss Association: ARIS
- **Team:** 100
- **Year:** 2018 Spaceport America Cup 10K
- **Score:** 525.0, ranked 57th
- **Predicted Apogee:** not specified
- **Apogee Reached:** not specified
- **Airbrake Type:** Pancake, 3 x 3200mm²
- **Control Method:** A look-up table made with Monte Carlo simulations considering various factors.
- **More on Control Method:** "The control values are chosen to minimize the risk of missing the target due to deviations from the simulation, choosing the 'path' closest to 10000ft. Once the risk is minimized, the algorithm also tries to minimize brake movement during each trajectory. The rocket's vertical position and velocity are calculated by integrating IMU measurements and barometer values, with a preference for IMU measurements during ascent due to biases in barometer values. The control table adjusts airbrakes based on the current position and altitude; if the rocket deviates from stored values, airbrakes are either fully extended or retracted."
- [Project Report](https://www.soundingrocket.org/uploads/9/0/6/4/9064598/100_project_report.pdf)

#### University of Ottawa
- **Team:** 55
- **Year:** 2018 Spaceport America Cup 10K
- **Score:** 510.0, ranked 59th
- **Predicted Apogee:** not specified
- **Apogee Reached:** not specified
- **Airbrake Type:** Pancake, 3 x 110.4cm²
- **Control Method:** Model Predictive Control (MPC), simulating the rocket in real-time to predict the final apogee and adjust airbrakes accordingly.
- [Project Report](https://www.soundingrocket.org/uploads/9/0/6/4/9064598/55_project_report.pdf)

#### Worcester Polytechnic Institute High Power Rocketry Club
- **Team:** 81
- **Year:** 2022 Spaceport America Cup 10K
- **Score:** 59th of 94 (Barrowman rank)
- **Predicted Apogee:** 10000ft
- **Apogee Reached:** 3854ft (due to flight failure)
- **Airbrake Type:** Pancake, 4 x 110.4cm²
- **Control Method:** Adjusts airbrakes to match real-time drag coefficients to calculated values using CFD analysis and OpenRocket simulations.
- [Technical Report](https://aiaa.wpi.edu/static/hprc/aquila/81_technical_report.pdf)

#### University of Maryland
- **Team:** 127
- **Year:** 2023 Spaceport America Cup 10K
- **Score:** 29th of 119 (Barrowman rank)
- **Predicted Apogee:** 10000ft
- **Apogee Reached:** 10473ft
- **Airbrake Type:** Flaps (deploy almost 90 degrees to body at max deployment), 29.9in²
- **Control Method:** Drag-modulating closed-feedback system.
- [Technical Report](https://drive.google.com/file/d/18ZheeMO8H3UuRlllgGhdWLznT8SM7l4D/view)

#### Duke University
- **Team:** 21
- **Year:** 2023 Spaceport America Cup 10K
- **Score:** 64th of 119 (Barrowman rank)
- **Predicted Apogee:** 10000ft
- **Apogee Reached:** 8279ft
- **Airbrake Type:** Pancake
- **Control Method:** Look-up table with pre-rendered flight simulations.
- [Project Poster](https://www.dukerocketry.com/static/sac_poster_2023-2be0677cc1351e5e15706fc27638b094.pdf)

#### University of Akron
- **Team:** 120
- **Year:** 2023 Spaceport America Cup 10K
- **Score:** 392, 86th of 101
- **Predicted Apogee:** 10000ft
- **Apogee Reached:** not specified
- **Airbrake Type:** Pancake, 3x 2.25 in²
- **Control Method:** Look-up table with pre-rendered flight simulations from OpenRocket and Ras Aero.
- [Flight Readiness Review Report](https://akronauts.files.wordpress.com/2018/03/university-of-akron-2018-frr-report.pdf)

## Literature
### SOURCE TITLE NAME
APA-FORMAT-CITATION-OF-SOURCE
- Key points

TODO

## Analysis of Literature
The field of amateur rocketry has seen significant advancements in
apogee control systems, particularly through the integration of
airbrakes. One such study by ARIS Space formulated the problem of apogee
targeting as a chance-constrained optimal control problem, addressing
challenges such as nonlinear dynamics and external disturbances like
wind. The study employed a three-step approach involving a reduced-order
model, offline problem-solving to generate a control table, and
real-time control during flight. This methodology allowed for the
offline computation of control policy, reducing the computational load
during the flight \[6\].

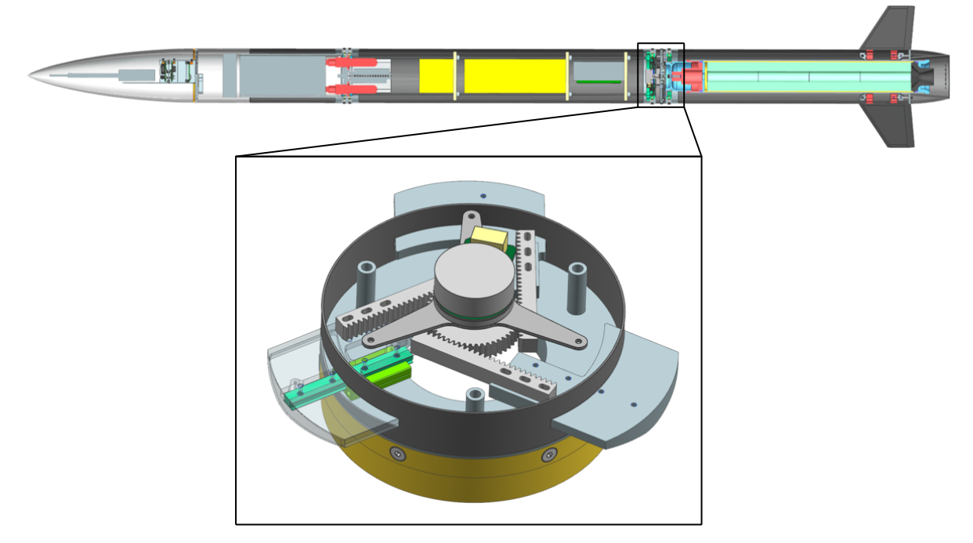
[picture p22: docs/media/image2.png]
A close-up of a mechanical device Description automatically generated

Another team aiming for precise apogee targeting in the Spaceport
America Cup used a SRAD rocket simulator along with a discrete PI
controller. Their airbrake design was positioned above the motor and
extended perpendicularly to the flight direction. The team conducted 3D
CFD analysis in ANSYS Fluent and used Monte Carlo simulations to produce
a normal distribution for optimal air brake deployment time \[7\].

The Queen\'s Rocket Engineering Team (QRET) developed an Active Rocket
Apogee Control (ARAC) system that also aimed for a 10,000 ft apogee.
Their design constraints included fitting within the tube of their
existing rocket and ensuring autonomous actuation. The system used
aerodynamic drag flaps actuated by a servomotor and controlled by an
on-board microcontroller. They also conducted Computational Fluid
Dynamics (CFD) and Finite Element (FE) analysis for flow physics and
structural integrity \[8\].

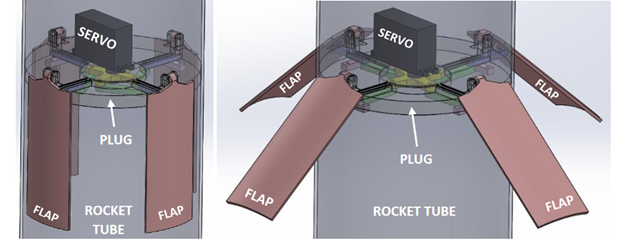
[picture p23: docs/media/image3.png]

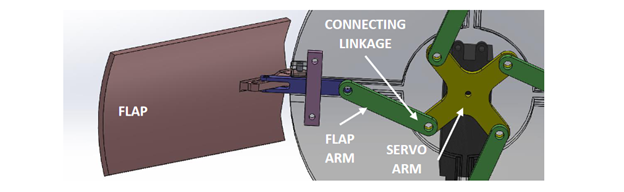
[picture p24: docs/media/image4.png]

Project EULER by ARIS Space in 2020 targeted a higher apogee of 30,000
feet. The project faced challenges with radial forces affecting
actuation and had to iterate their airbrake design. Despite a parachute
failure that led to rocket destruction, telemetry and accelerometer data
confirmed successful airbrake deployment \[9\]. 

A close up of a pen Description automatically generated
A heat map of a pipe Description automatically generated with medium confidence
ThrustMIT focused on designing a low-cost airbrake system. They employed
a 4th-order Runge-Kutta method for real-time apogee prediction and used
a Teensy 4.1 microcontroller for high computational power. The airbrakes
were made of aluminum and designed to withstand high forces. Safety
measures included a virtual floor of 5000ft to prevent unwanted
deployment \[10\]. 

A collage of images of a mechanical device Description automatically generated

Another paper by ThrustMIT presents an optimization method for the
Runge-Kutta 4th Order Method used as part of the control scheme. This
Neural Network-based optimization technique aimed to improve
computational efficiency and allow a higher number of predictions during
the control period. The Neural Network was trained on data generated
from traditional RK4 simulations and could predict the airbrake state in
real-time \[11\].

The 10,000ft airbrakes system adopted by ARIS in 2018 uses three control
surfaces oriented perpendicularly to the roll axis to modulate drag,
activated by a servo motor based on sensor feedback, to fine-tune ascent
dynamics. The control strategy is supported by a software framework
comprising a trajectory simulator for validation and planning, dynamic
programming for optimal trajectory planning, an online control algorithm
that adjusts air brakes in real-time based on IMU and barometer data,
and a verification module that tests the system\'s reliability against
various failure scenarios. The IMU readings were prioritized during
ascent phase as it was found that test flights yielded a bias in the
barometer readings for high velocities \[12\]. This bias could be
attributed to the requirement for properly sized and tested pressure
ports \[13\], \[14\].
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

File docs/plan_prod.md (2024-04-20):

# Production Planning

## Mechanical Prototype Development

For the entirety of the first semester all design choices were made
assuming four flaps were being used. Unfortunately, soon after the
Christmas break and in early January the rocketry team changed from four
fins on the rocket to three fins which necessitated a change to three
flaps from the original four. This initially was not deemed as creating
a significant change for the airbrake team by the rocketry team however
once it was further investigated this was not the case. Due to this
change the entire design of the airbrake system had to be re-done from
the ground up starting with all new part files without a single part
being transferrable to the new three flap design. Clearly this had a
large impact on the timeline and prototyping process as many of the
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

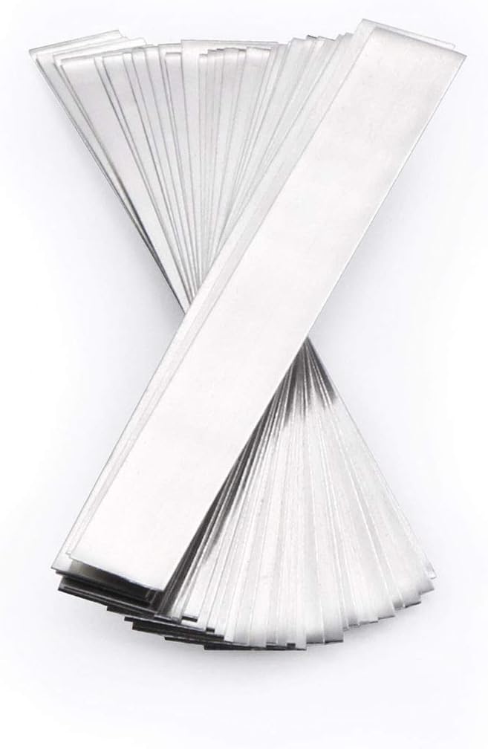
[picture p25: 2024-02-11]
mechanical/CAD/battery_pack_scad/images/nickel_battery_strips.jpg

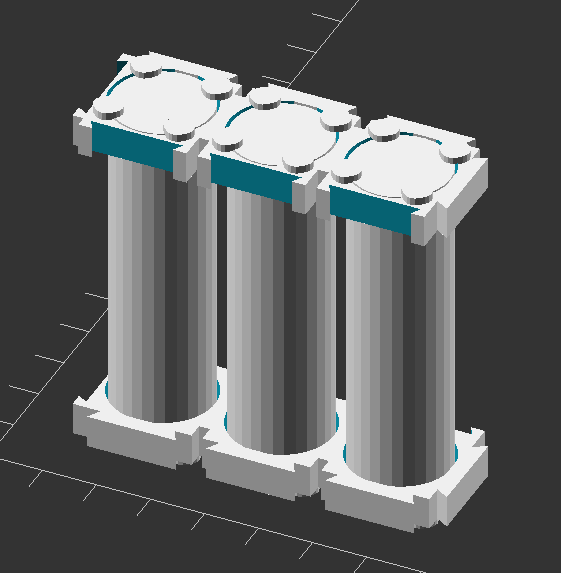
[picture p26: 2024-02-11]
mechanical/CAD/battery_pack_scad/images/battery_assem_x3.png

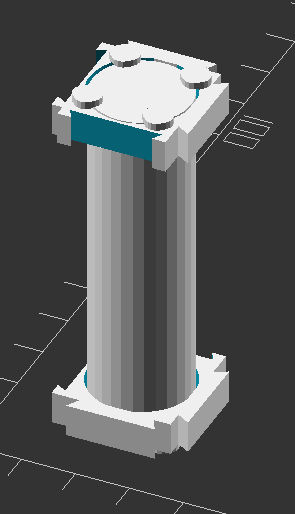
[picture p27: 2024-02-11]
mechanical/CAD/battery_pack_scad/images/battery_assem_x1.png

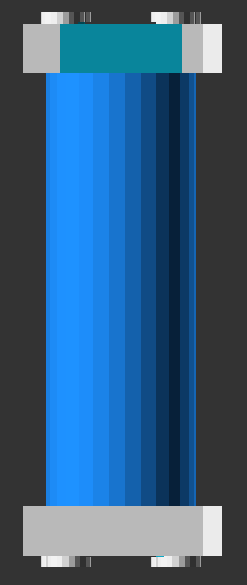
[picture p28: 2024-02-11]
mechanical/CAD/battery_pack_scad/images/battery_assem_x1_blue-top.png

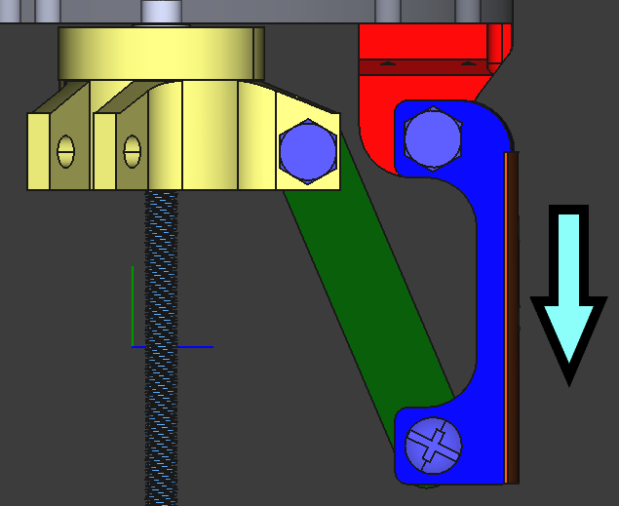
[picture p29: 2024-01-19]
mechanical/internal_loading_pics/static_arm_0deg.png

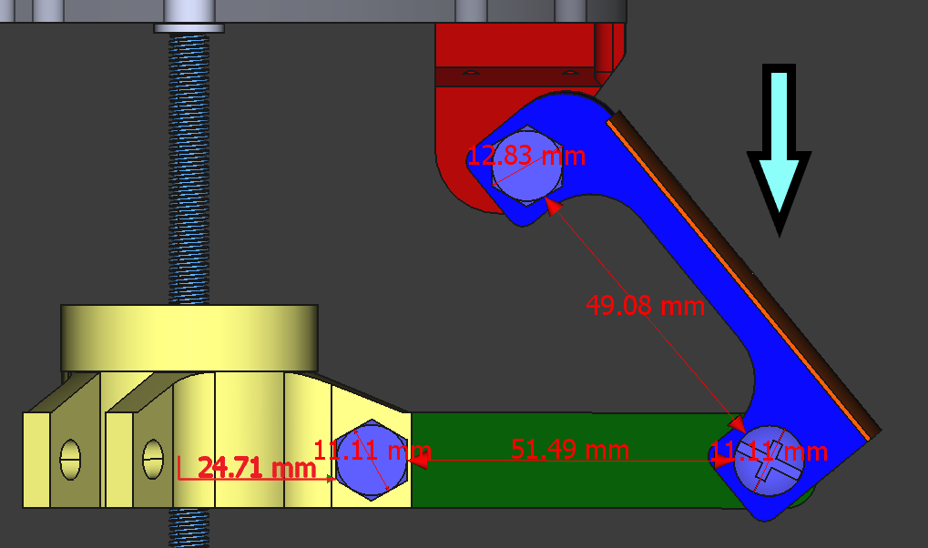
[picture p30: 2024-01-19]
mechanical/internal_loading_pics/static_arm_45deg.png

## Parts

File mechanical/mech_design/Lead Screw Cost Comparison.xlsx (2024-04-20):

1/4 - 16 (28 revs) |  |  |  |  | Assumptions
Item | Link | Price | Total
Lead Screw | https://www.mcmaster.com/99030A981 | 20.2 | $127.37
Lead Nut | https://www.mcmaster.com/95072A881 | 36.04
Flange Nut | https://www.mcmaster.com/1329K11 | 56.48
1/4 -12 (21 revs) |  |  |  | WINNER
Item | Link | Price | Total
Lead Screw | https://www.mcmaster.com/99030A978 | 10.72 | $124.37
lead Nut | https://www.mcmaster.com/95072A107 | 61.28
Flange Nut | https://www.mcmaster.com/95082A641 | 38.06
1/4 - 8 (14 revs)
Item | Link | Price | Total
lead Screw | https://www.mcmaster.com/6350K701 | 164.23 | $214.24
Lead nut | https://www.mcmaster.com/6350K32 | 25.36

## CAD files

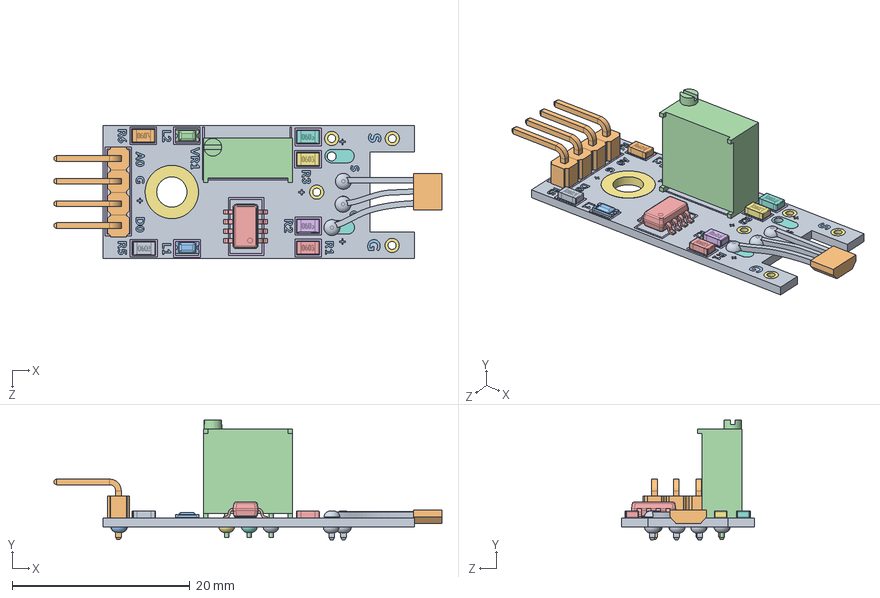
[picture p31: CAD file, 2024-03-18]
mechanical/CAD/components-electrical-ardupro/hall-effect-sensor/Linear Magnetic Hall Effect Switches.SLDASM
43.6 x 13.4 x 15.0 mm
Pins.step
Sensor-0.step
Fusion002.step
Trimpot.step
lm393.step
Pad003.step
Pad001.step
Pad002.step
PCB.step
PIN HEADER, 1X4, 2.54 mm.step
Led.step
Led (1).step
Resistor.step
Resistor (1).step
Resistor (2).step
Resistor (3).step
Resistor (4).step
Resistor (5).step
Pad (2).step
Pad (4).step
Pad (3).step
Pad (5).step
Pad (2) (1).step
Pad (2) (2).step
Pad (2) (3).step x 7
Pad.step
Pad (1).step
Pad (6).step

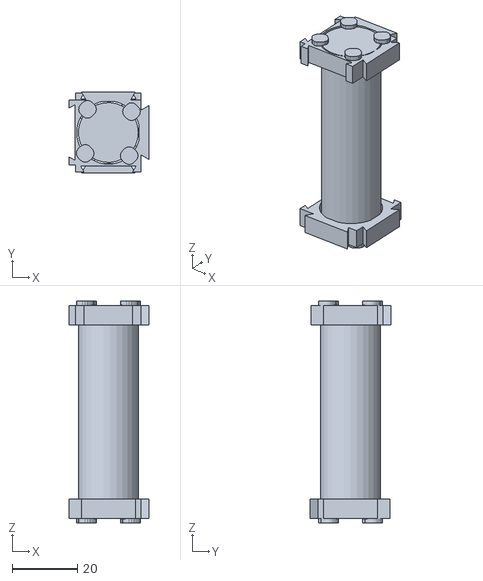
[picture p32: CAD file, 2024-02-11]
mechanical/CAD/battery_pack_scad/stl/battery_assem-x1.stl
24.4 x 24.8 x 67.8

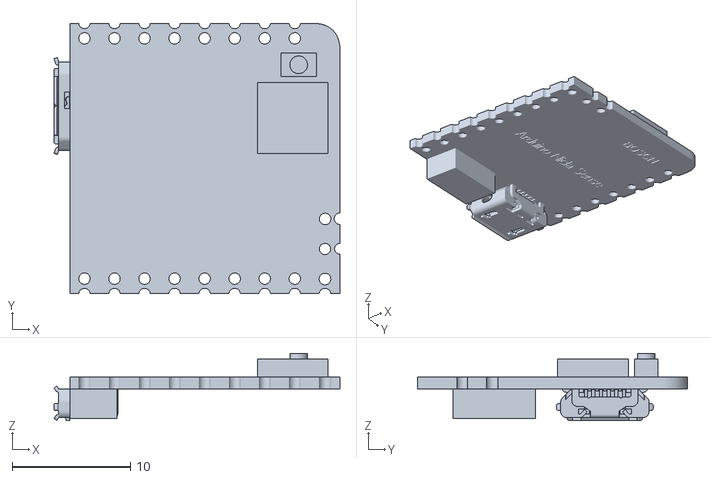
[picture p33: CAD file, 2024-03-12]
mechanical/CAD/components-electrical-ardupro/arduino-nicla-sense-me/Nicla Sense v4.stl
24.2 x 22.9 x 5.70

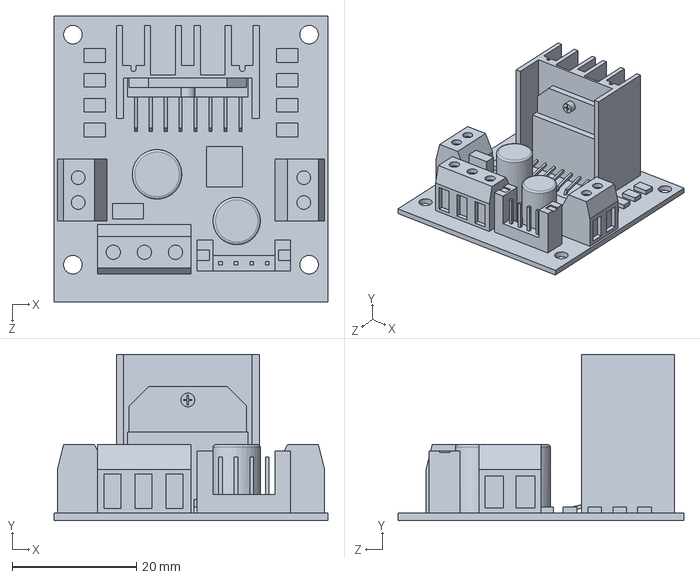
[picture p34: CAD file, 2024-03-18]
mechanical/CAD/components-electrical-ardupro/motor-driver-l298n/MOTOR_DRIVER_L298N.SLDPRT
44.0 x 26.7 x 46.0 mm

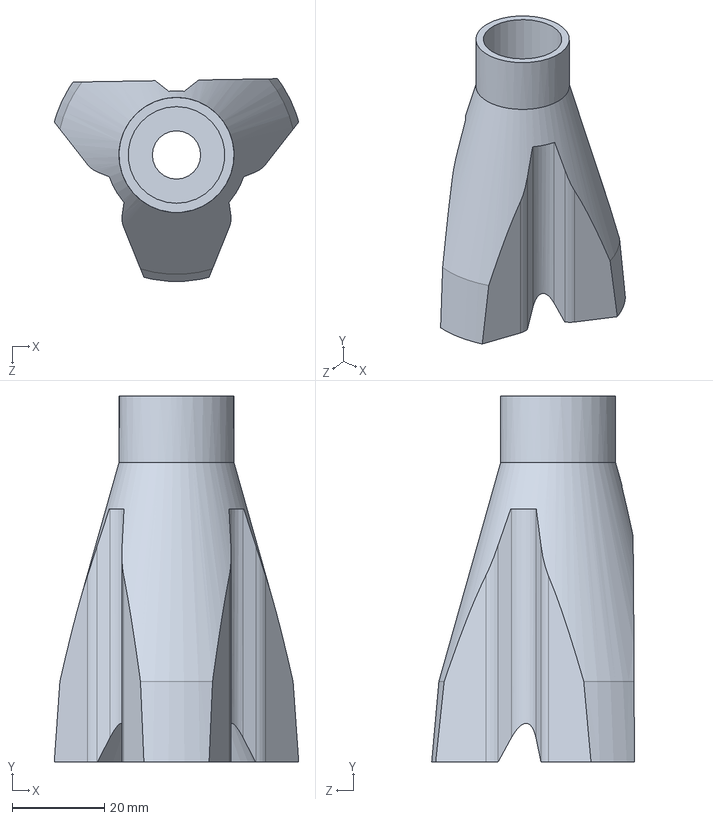
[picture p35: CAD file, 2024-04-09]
mechanical/CAD/airbrakes_CAD_V5_0_0/Motor Platform.SLDPRT
53.1 x 79.5 x 44.0 mm

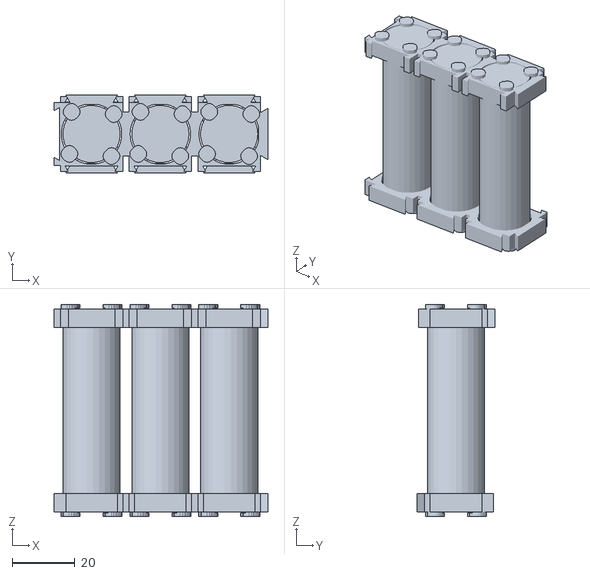
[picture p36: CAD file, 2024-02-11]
mechanical/CAD/battery_pack_scad/stl/battery_assem_x3.stl
68.4 x 24.8 x 67.8

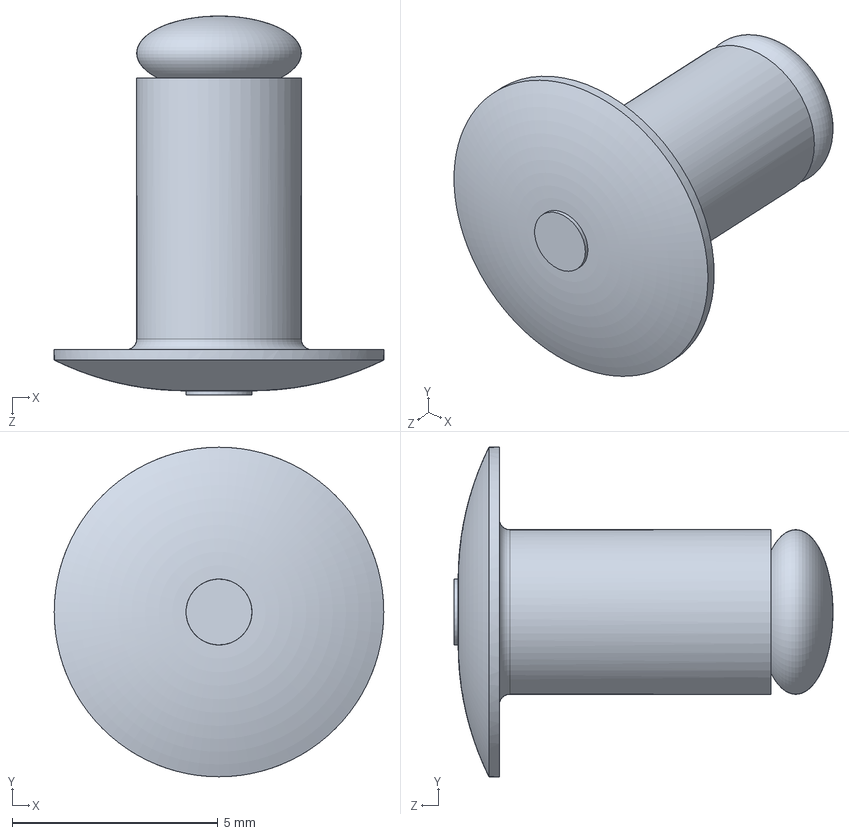
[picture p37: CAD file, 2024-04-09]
mechanical/CAD/airbrakes_CAD_V5_0_0/Rivet Pressed.SLDPRT
8.00 x 8.00 x 9.20 mm

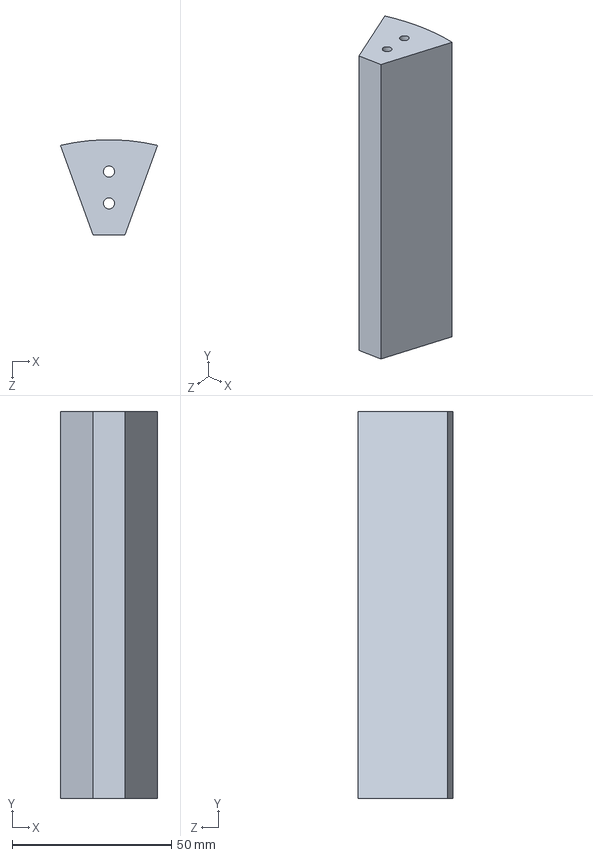
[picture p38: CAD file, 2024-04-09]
mechanical/CAD/airbrakes_CAD_V5_0_0/Platform Spacers.SLDPRT
30.5 x 121.7 x 30.0 mm

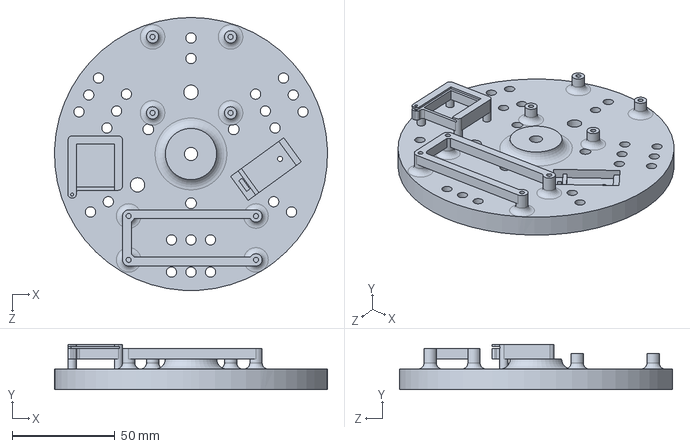
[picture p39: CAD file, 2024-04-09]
mechanical/CAD/airbrakes_CAD_V5_0_0/Shell Epoxy Platform.SLDPRT
132.9 x 22.0 x 133.0 mm

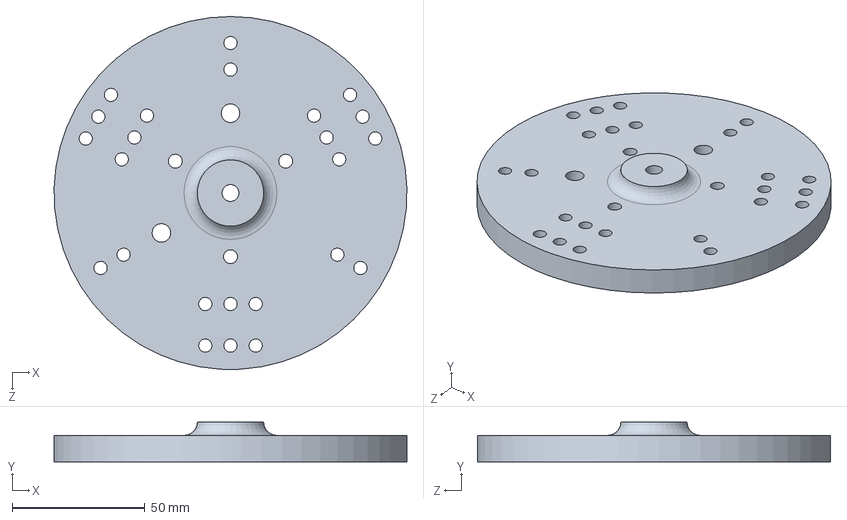
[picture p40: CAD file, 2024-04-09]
mechanical/CAD/airbrakes_CAD_V5_0_0/Shell Epoxy Platform - No Standoffs.SLDPRT
132.9 x 15.0 x 133.0 mm

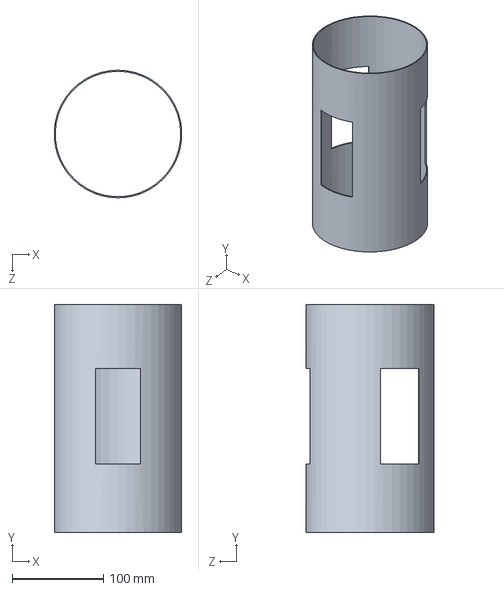
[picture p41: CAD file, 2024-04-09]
mechanical/CAD/airbrakes_CAD_V5_0_0/Rocket Shell - 3.SLDPRT
139.7 x 250.0 x 140.0 mm

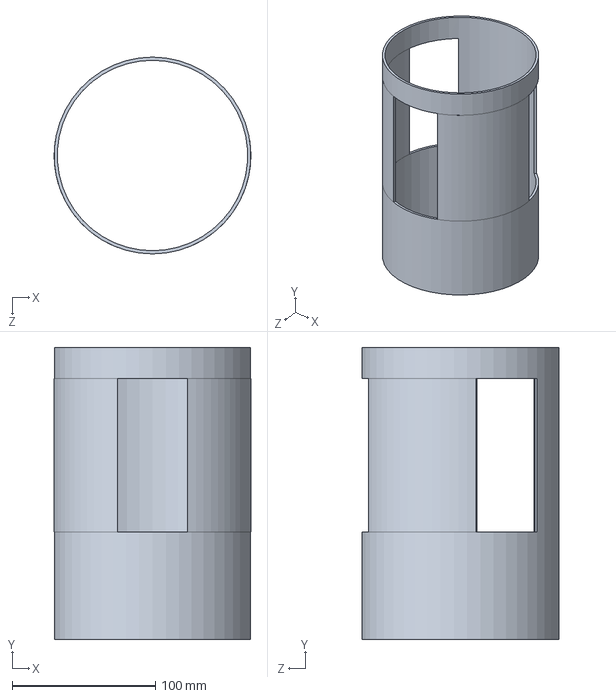
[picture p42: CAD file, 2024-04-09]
mechanical/CAD/airbrakes_CAD_V5_0_0/Coupler tube.SLDPRT
137.5 x 204.0 x 137.5 mm

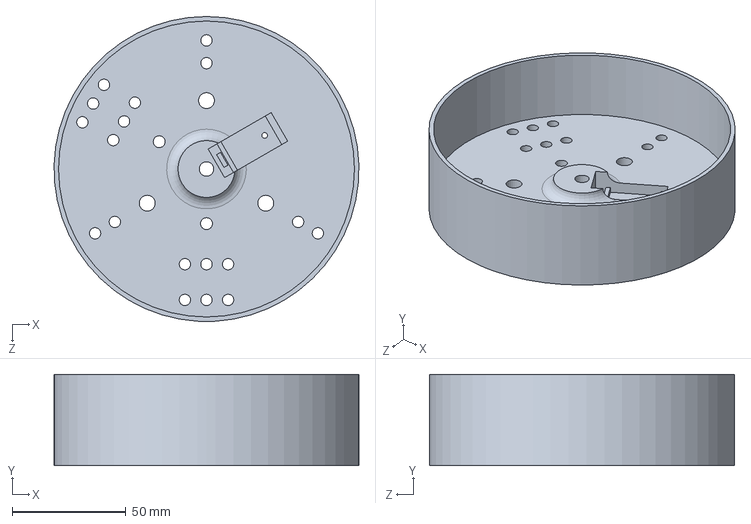
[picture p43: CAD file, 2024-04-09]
mechanical/CAD/airbrakes_CAD_V5_0_0/Bottom Platform.SLDPRT
133.9 x 40.0 x 134.0 mm

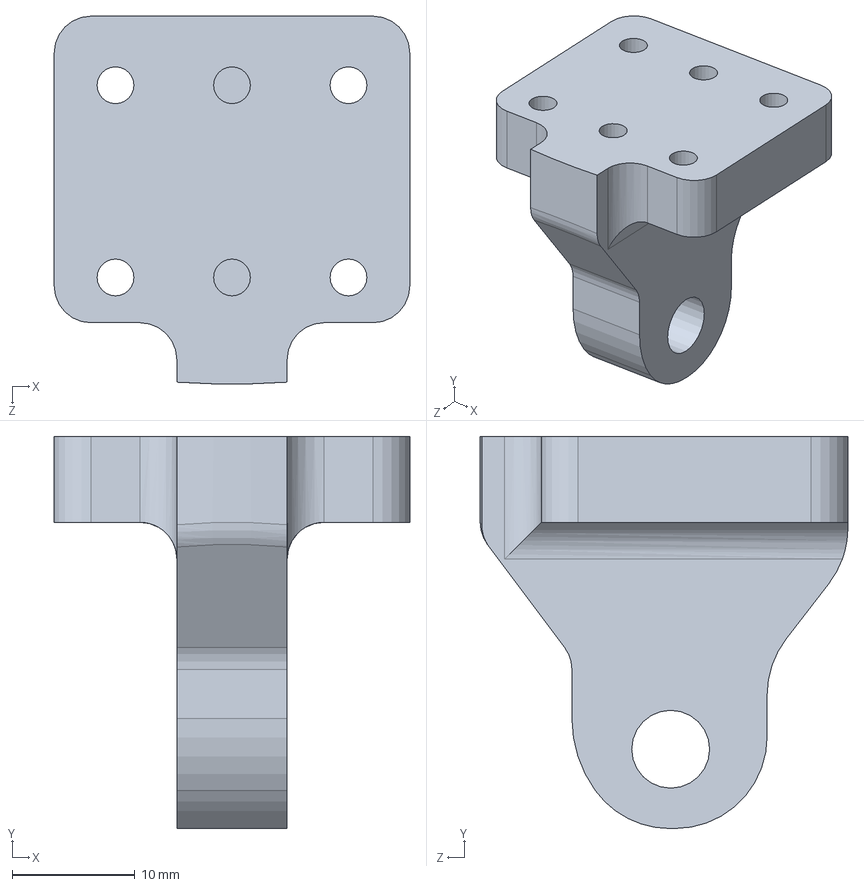
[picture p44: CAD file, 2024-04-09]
mechanical/CAD/airbrakes_CAD_V5_0_0/Top Hinge.SLDPRT
29.0 x 32.0 x 30.0 mm

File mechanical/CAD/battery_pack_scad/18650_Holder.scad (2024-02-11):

// Improved, modular version of the 18650 battery holder script
// Based on https://www.thingiverse.com/thing:3026658

// Constants
diameter = 18.8; // Diameter of 18650 cell
height = 6;      // Height of holder
tab = 1.4;       // Tab height
tolerance = 0.5; // Tolerance to help fit

// Main configuration module
module batteryHolderConfig(cells_x = 2, cells_y = 2, negative = 0, cable_tie = 1) {
    // Generate the grid of cells and connectors
    generateCells(cells_x, cells_y, negative, cable_tie, diameter, height, tab);
    generateGaps(cells_x, cells_y, cable_tie, height);
    generateConnectors(cells_x, cells_y, height, tolerance, cable_tie);
}

// Generates the grid of cells
module generateCells(cells_x, cells_y, negative, cable_tie, diameter, height, tab) {
    for ( y= [1:1:cells_y]) for ( x= [ 1:1:cells_x]) 
        translate ([x*22,y*22,0]) cell(diameter, height, tab, negative);
}

// Fills gaps between cells
module generateGaps(cells_x, cells_y, cable_tie, height) {
    for ( x= [1:1:cells_x]) for ( y= [1:1:cells_y-1])    
        translate([22*x- (cable_tie ==1 ? 7: 12),22*y+10,0]) cube([cable_tie ==1 ? 14 : 22,2,height]);

    for ( x= [1:1:cells_x-1]) for ( y= [1:1:cells_y])    
        translate([22*x+12,22*y-(cable_tie ==1 ? 7: 10),0]) rotate([0,0,90]) cube([cable_tie ==1 ? 14: 22,2,height]);
}

// Adds male and female connectors
module generateConnectors(cells_x, cells_y, height, tolerance, cable_tie) {
    for ( x= [1:1:cells_x]) translate([22*x,22*cells_y+11.4,0]) trapezoid(13, height);
    for ( y= [1:1:cells_y]) translate([22*cells_x+11.4,22*y,0]) rotate([0,0,-90]) trapezoid(13, height);
    
    for ( x= [1:1:cells_x]) difference() {
        translate([22*x,11,height/2])cube([20,2,height],center=true);
        translate([22*x,10.8,0]) trapezoid(13+tolerance, height);
    }
    for ( y= [1:1:cells_y]) difference() {
        rotate([0,0,90]) translate([22*y,-11,height/2])cube([20,2,height],center=true);
        rotate([0,0,90]) translate([22*y,-10.8,0]) rotate([0,0,180]) trapezoid(13+tolerance, height);
    }
}

// Module for trapezoid (connectors)
module trapezoid(length, height) {
    hull() { 
        translate([-length/2, 0, 0]) rotate([0,0,30]) cylinder (r = 2, h=height,  $fn=3); 
        translate([length/2, 0, 0]) rotate([0,0,30]) cylinder (r = 2, h=height,  $fn=3);
    }
}

// Module to create a single cell
module cell(diameter, height, tab, negative) {
    difference() {
        union() {
            translate([0,0,height/2]) cube([20,20,height],center = true);
            if (!negative) for (rotation =[45:90:325]) rotate([0,0,rotation])  
                translate([0,9,0]) hull(){     
                    translate([1,0,height]) cylinder(r=2, h=tab, $fn=16);
                    translate([1,1,height]) cylinder(r=2, h=tab, $fn=16);
                    translate([0,1,height]) cylinder(r=2, h=tab, $fn=16);
                    translate([0,0,height]) cylinder(r=2, h=tab, $fn=16);
                } 
        }
        rotate([0,0,-0.1]) cylinder(r=diameter/2 + tolerance/2, h= height+ 0.2, $fn=64); // Hole for cell
    }
}

// Example usage:
batteryHolderConfig(cells_x = 3, cells_y = 2, negative = 1, cable_tie = 1);

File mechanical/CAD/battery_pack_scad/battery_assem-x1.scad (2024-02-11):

use <18650_Holder.scad>;
use <battery_lib.scad>

translate([0, 0, 10]) {
// Generate a model of a tube battery 
translate([22, 22, 0]) 
color("DodgerBlue") BatteryLib_GenerateBatteryModel("18650");


translate([0, 44, 6]) 
rotate([180, 0, 0]) 
batteryHolderConfig(cells_x = 1, cells_y = 1, negative = 0, cable_tie = 1);

translate([0, 0, 59]) 
batteryHolderConfig(cells_x = 1, cells_y = 1, negative = 0, cable_tie = 1);
}

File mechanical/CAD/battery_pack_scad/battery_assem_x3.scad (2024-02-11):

use <18650_Holder.scad>;
use <battery_lib.scad>

// Generate a model of a tube battery 
translate([22, 22, 0]) 
color("DodgerBlue") BatteryLib_GenerateBatteryModel("18650");

translate([44, 22, 0]) 
color("DodgerBlue") BatteryLib_GenerateBatteryModel("18650");

translate([66, 22, 0]) 
color("DodgerBlue") BatteryLib_GenerateBatteryModel("18650");

translate([0, 44, 6]) 
rotate([180, 0, 0]) 
batteryHolderConfig(cells_x = 3, cells_y = 1, negative = 0, cable_tie = 1);

translate([0, 0, 59]) 
batteryHolderConfig(cells_x = 3, cells_y = 1, negative = 0, cable_tie = 1);

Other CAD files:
mechanical/mech_design/CF_forged_flaps/mould_V1/Mould Top.STEP
mechanical/CAD/components-electrical-ardupro/arduino-nicla-sense-me/Nicla Sense.step
mechanical/mech_design/CF_forged_flaps/mould_V1/Mould Base.STEP
mechanical/CAD/airbrakes_CAD_V5_0_0/Flap Support.SLDPRT
mechanical/CAD/battery_pack_scad/battery_lib.scad
mechanical/CAD/airbrakes_CAD_V5_0_0/6338K563_Oil-Embedded Flanged Sleeve Bearing.SLDPRT
mechanical/CAD/airbrakes_CAD_V5_0_0/94622A215_Cadmium-Plated Steel Hex Head Screw.SLDPRT
mechanical/CAD/airbrakes_CAD_V5_0_0/94887A363_Low-Profile Binding Barrels and Screws.SLDPRT
mechanical/CAD/airbrakes_CAD_V5_0_0/95075A340_Plastic Externally Threaded Precision Acme Nut.SLDPRT
mechanical/CAD/airbrakes_CAD_V5_0_0/95082A641_Precision Acme Flange.SLDPRT
mechanical/CAD/airbrakes_CAD_V5_0_0/97763A431_18-8 Stainless Steel Button Head Hex Drive Screws.SLDPRT
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

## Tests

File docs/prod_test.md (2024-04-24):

# Production & Testing

## Testing

### Tube Crushing

The principal concern in meeting the requirement to survive loading at
max-g was whether the portion of the airframe containing the cutouts for
the flaps would be strong enough to transfer thrust through that section
of the rocket. The other components of the airbrakes system don't
transfer thrust along the rocket and are not of concern.

The thrust that needs to be transferred through the part of the airframe
containing the airbrakes is equal to the force required to accelerate
the mass at and above the airbrakes system with the maximum acceleration
that the rocket will experience (which occurs during its motor burn when
the airbrakes are not deployed, specifically at the moment when the
motor hits its peak thrust of 2938 N). As reported in Section 11.4.5,
the maximum acceleration is projected to be 13.58 g. The mass at and
above the airbrakes system is 11.63 kg. The total thrust transferred
through the airbrakes to the upper portion of the rocket is the mass
required to accelerate 11.63 kg at 13.58 g (133 m/s^2^), which by
Newton's Second Law is 1547 N.

A tube manufactured by WE Rocketry's aerostructures team with holes cut
into it where the airbrake flaps would extend through was compression
tested until failure in Western's Tensile Testing Laboratory to
determine if the section of body tube on the final rocket with holes cut
in it for the flaps to go through would be able to withstand the loads
it will experience at the moment of maximum thrust transfer.

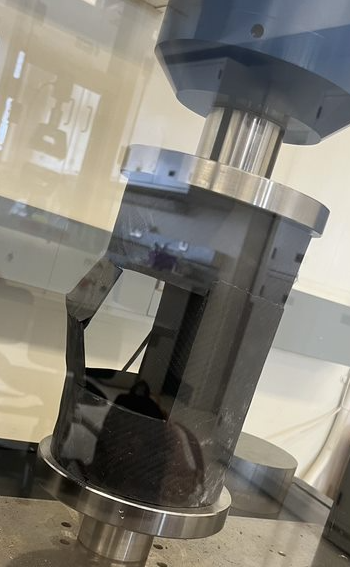
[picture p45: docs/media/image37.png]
A close up of a machine Description automatically generated


There was a marked (though not unexpected) difference in the strength of
the tube with the cutouts compared to the tubes without the cutouts. The
tube without the cutouts could withstand a compressive force of 11.16
kN, compared to the tube with the cutouts, which could only withstand a
compressive force of 2.37 kN. The stress-strain curves for the two tubes
are shown below in Figure 33 and Figure 34.

The lower strength of the tube with the cutouts does not pose a risk to
the safety of the system. The factor of safety of 1.53 is sufficient for
several reasons:

1.  The factors that define the expected load used in the factor of
    safety calculation are well defined:

    a.  The thrust curve and mass burn rate of the motor of the rocket.
        The team is using a COTS motor and is confident that the motor
        will be within its specification, with a maximum variation of up
        to a few percent.

    b.  The mass of the components in the rocket may be less than
        currently estimated by the time the rocket is complete. However,
        the rocket's mass incredibly unlikely to change by more than a
        couple of percent between current estimates of the final mass
        and launch.

2.  The tube chosen for the testing was the first and worst-quality tube
    that the WE Rocketry aerostructures team has made this year. It was
    oversaturated with resin and had a poor surface finish with many
    bumps and ridges. The body tube chosen for the final airframe will
    be of significantly better quality, and thus stronger.

3.  The holes cut into the tube were significantly oversized compared to
    the holes that will be cut into the actual body tube that flies on
    the rocket. This was done because the final flap size had not been
    settled on at the time of the compression testing, so larger holes
    were chosen as a worst-case scenario.

### Actuation Testing

The actuation of the mechanism was tested after electromechanical
integration to assess the motion and performance. The motor was
successfully able to drive the unloaded mechanism well within the
required time taking only 1.51 seconds from top to bottom. However,
during the loaded testing discussed in the following section, the motor
could only actuate in the approximate upper and lower 30% of the lead
screw and stalled at the center point. This indicates that the force
model and subsequent motor selection should be revisited and the motor
selection reassessed. An analogous model of motor from the same
manufacturer has been ordered in the size up for future preliminary
testing.

### Loaded Testing

The system was tested with the flaps loaded to the maximum expected
loads they would see during flight. The mechanical assembly successfully
supported the maximum expected flight loads, as can be seen in Figure
35:

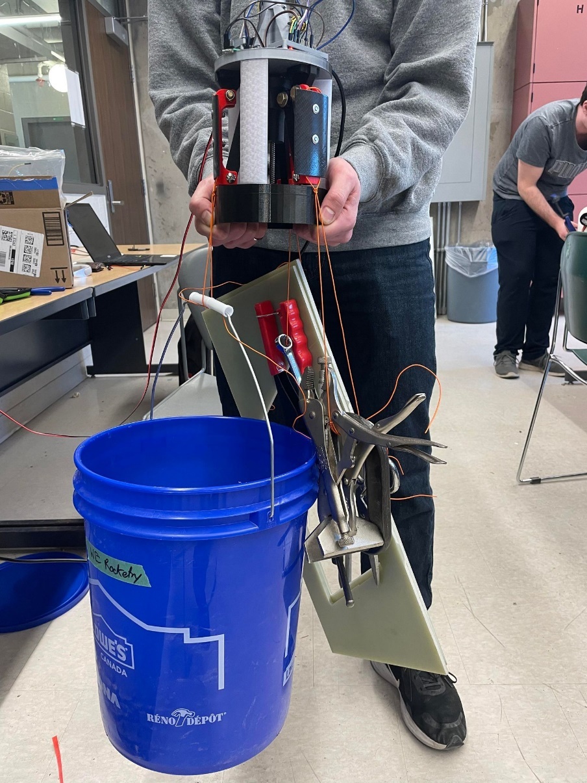
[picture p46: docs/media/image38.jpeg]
No description available.


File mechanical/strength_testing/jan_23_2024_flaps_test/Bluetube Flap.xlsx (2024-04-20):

Applied Load [kg] | Observations | Bucket and clamp | 1.36 | kg | Expected load on 1 flap | 75 | N | from sims
4.122 | bending |  |  |  |  | 7.645259939
6.896 | bending | Dimensions: |  |  | FoS | 3.1719
9.456 | bending | radius: 5.5"
12.138 | bending | length: 6.5cm
24.25 | bending, permanent deformation

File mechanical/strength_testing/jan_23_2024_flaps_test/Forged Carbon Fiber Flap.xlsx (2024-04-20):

Applied Load [kg] | Observations | Bucket and clamp |  | 1.36 | kg | expected load on flap | 75 | N | from sims
4.126 |  |  |  |  |  |  | 7.645259939
6.904 |  |  |  |  |  | FoS | 7.1762112
9.462 | Flap is bending under load
12.144 | Flap is bending under load
25.064 | Flap is bending under load, some cracking is heard | Ratio
29.8 | bending, cracking sounds, approx mass | 18.5 cm | 29.80583784
54.864 | bending, some cracking, approx mass | 22cm
Date of test: | Jan 23rd | Flap dimensions:

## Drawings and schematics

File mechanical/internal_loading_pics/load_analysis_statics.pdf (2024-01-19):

A

## Tony

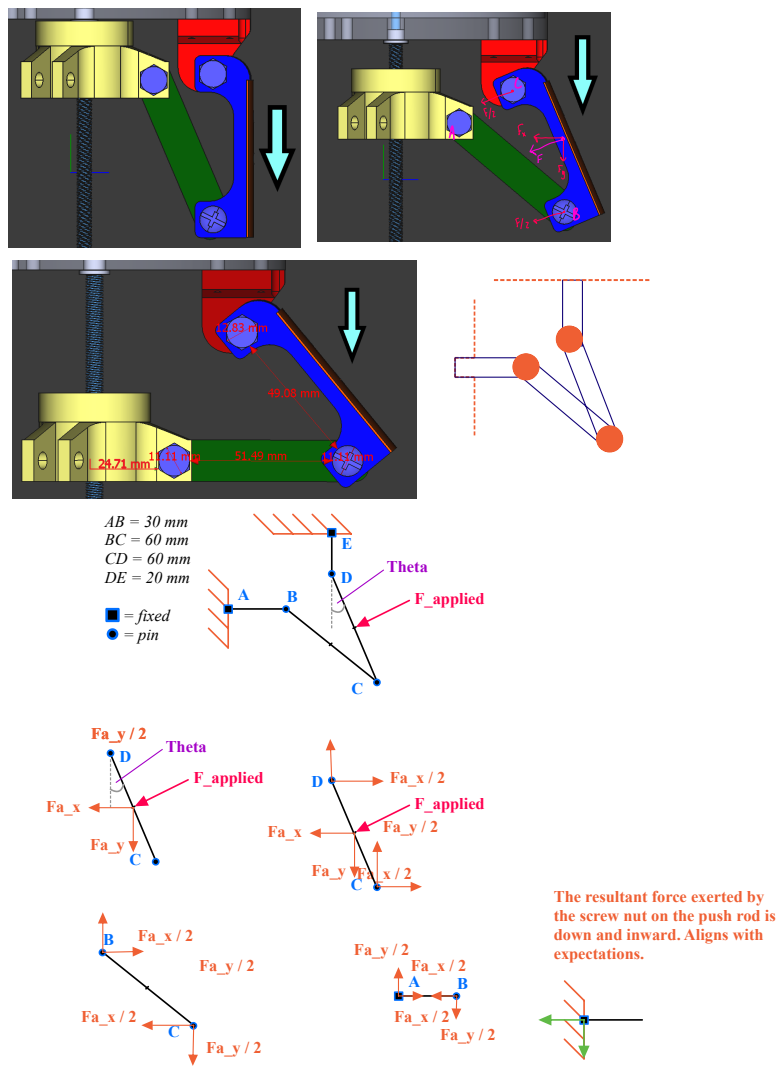
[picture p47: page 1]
F_applied; Theta; = fixed = pin

The resultant force exerted by
the screw nut on the push rod is
down and inward. Aligns with
expectations.

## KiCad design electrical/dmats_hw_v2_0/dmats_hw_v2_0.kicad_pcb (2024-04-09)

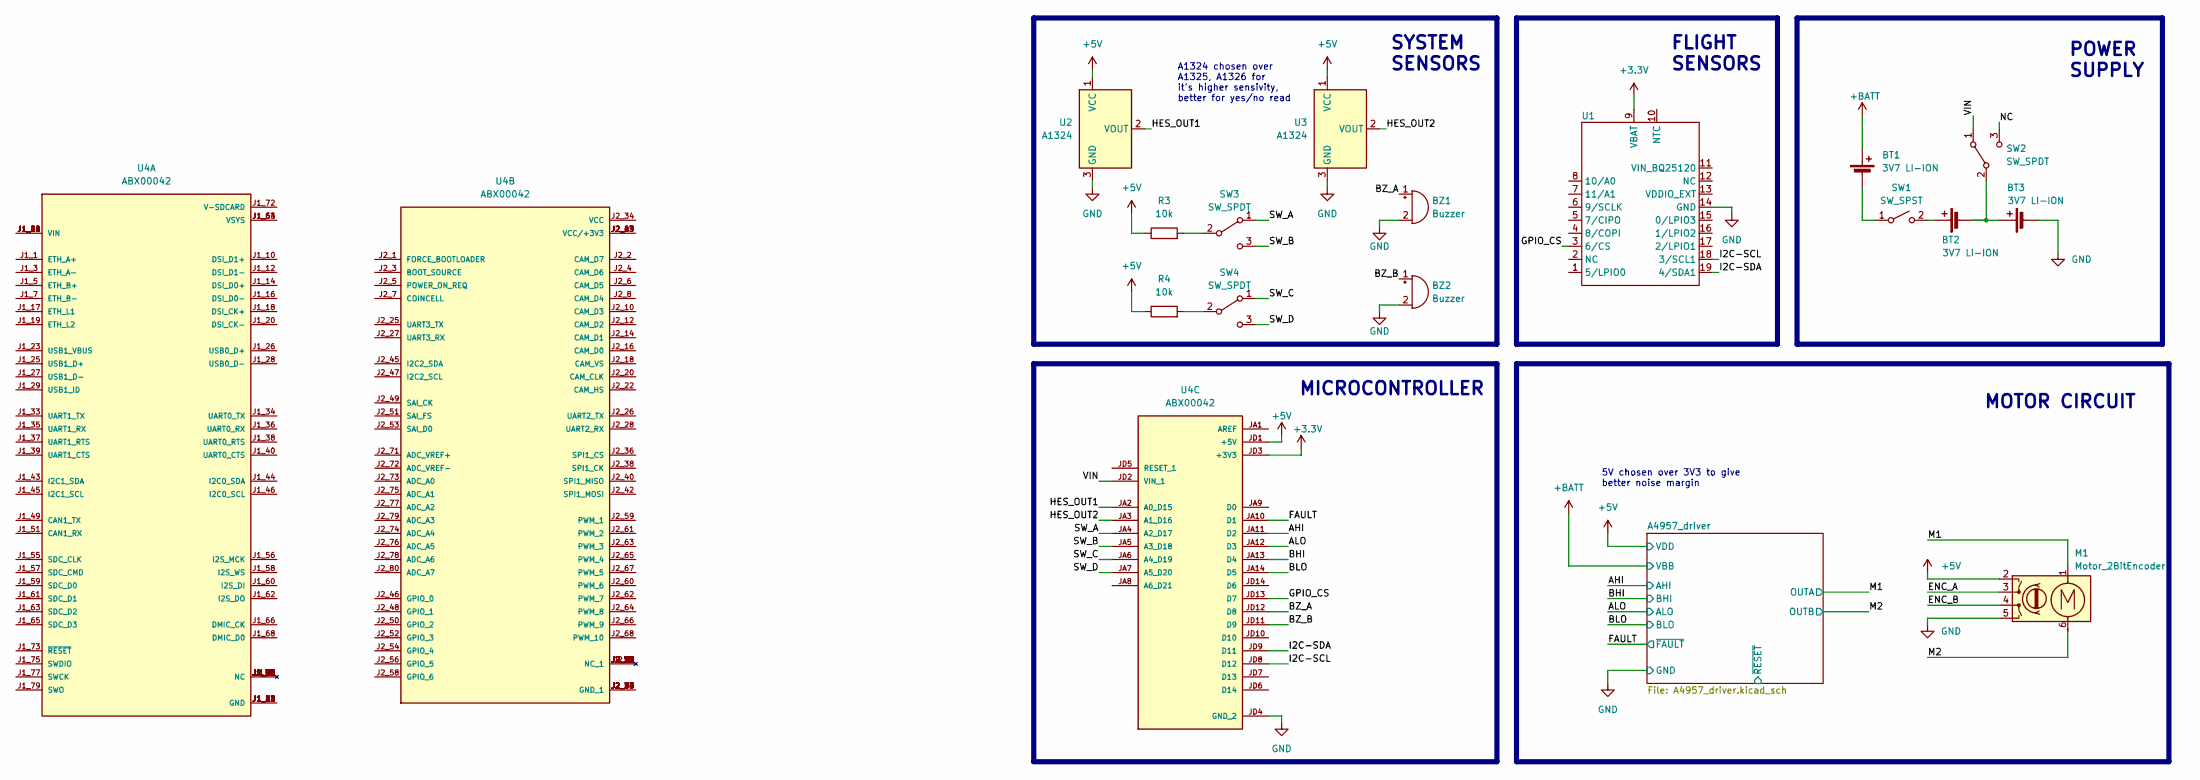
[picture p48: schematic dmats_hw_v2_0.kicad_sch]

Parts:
BT1, BT2, BT3: 3V7 LI-ION; BatteryHolder_Keystone_1042_1x18650
BZ1, BZ2: Buzzer; Buzzer_12x9.5RM7.6
M1: Motor_2BitEncoder; JST_PH_B6B-PH-K_1x06_P2.00mm_Vertical
R3, R4: 10k; R_0603_1608Metric
SW1: SW_SPST; SW_DIP_SPSTx01_Slide_Power
SW2, SW3, SW4: SW_SPDT; CUI_SLW-913535-2A-RA-D_SPDT_Angled
U1: ARDUINO_NICLA
U2, U3: A1324; JST_EH_S3B-EH_1x03_P2.50mm_Horizontal
U4: ABX00042; MODULE_ABX00042; PARTREV 2

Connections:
+3.3V: U1.9 (VBAT), U4.JD3 (+3V3)
+5V: M1.2 (VCC), R3.1, R4.1, U2.1 (VCC), U3.1 (VCC), U4.JD1 (+5V); also elsewhere on the board
+BATT: BT1.1 (+); also elsewhere on the board
/AHI: U4.JA11 (D2); also elsewhere on the board
/ALO: U4.JA12 (D3); also elsewhere on the board
/BHI: U4.JA13 (D4); also elsewhere on the board
/BLO: U4.JA14 (D5); also elsewhere on the board
/BZ_A: BZ1.1 (-), U4.JD12 (D8)
/BZ_B: BZ2.1 (-), U4.JD11 (D9)
/ENC_A: M1.3 (C2)
/ENC_B: M1.4 (C1)
/FAULT: U4.JA10 (D1); also elsewhere on the board
/GPIO_CS: U1.3 (6/CS), U4.JD13 (D7)
/HES_OUT1: U2.2 (VOUT), U4.JA2 (A0_D15)
/HES_OUT2: U3.2 (VOUT), U4.JA3 (A1_D16)
/I2C-SCL: U1.18 (3/SCL1), U4.JD8 (D12)
/I2C-SDA: U1.19 (4/SDA1), U4.JD9 (D11)
/M1: M1.1 (M1); also elsewhere on the board
/M2: M1.6 (M2); also elsewhere on the board
/NC: SW2.3 (C)
/SW_A: SW3.1 (A), U4.JA4 (A2_D17)
/SW_B: SW3.3 (C), U4.JA5 (A3_D18)
/SW_C: SW4.1 (A), U4.JA6 (A4_D19)
/SW_D: SW4.3 (C), U4.JA7 (A5_D20)
/VIN: SW2.1 (A), U4.JD2 (VIN_1)
GND: BT3.2 (-), BZ1.2 (+), BZ2.2 (+), M1.5 (GND), U1.14 (GND), U2.3 (GND), U3.3 (GND), U4.JD4 (GND_2); also elsewhere on the board
unnamed: BT1.2 (-), SW1.1 (A)
unnamed: BT2.1 (+), SW1.2 (B)
unnamed: BT2.2 (-), BT3.1 (+), SW2.2 (B)
unnamed: R3.2, SW3.2 (B)
unnamed: R4.2, SW4.2 (B)
unnamed: U4.J1_22 (GND), U4.J1_31 (GND), U4.J1_42 (GND), U4.J1_47 (GND), U4.J1_54 (GND)
unnamed: U4.J1_21 (VIN), U4.J1_32 (VIN), U4.J1_41 (VIN), U4.J1_48 (VIN)
unnamed: U4.J1_53 (VSYS), U4.J1_64 (VSYS)
unnamed: U4.J2_24 (GND_1), U4.J2_33 (GND_1), U4.J2_44 (GND_1), U4.J2_57 (GND_1), U4.J2_70 (GND_1)
unnamed: U4.J2_23 (VCC/+3V3), U4.J2_43 (VCC/+3V3), U4.J2_69 (VCC/+3V3)

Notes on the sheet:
SYSTEM SENSORS
FLIGHT SENSORS
POWER SUPPLY
MICROCONTROLLER
MOTOR CIRCUIT
5V chosen over 3V3 to give better noise margin
A1324 chosen over A1325, A1326 for it's higher sensivity, better for yes/no read

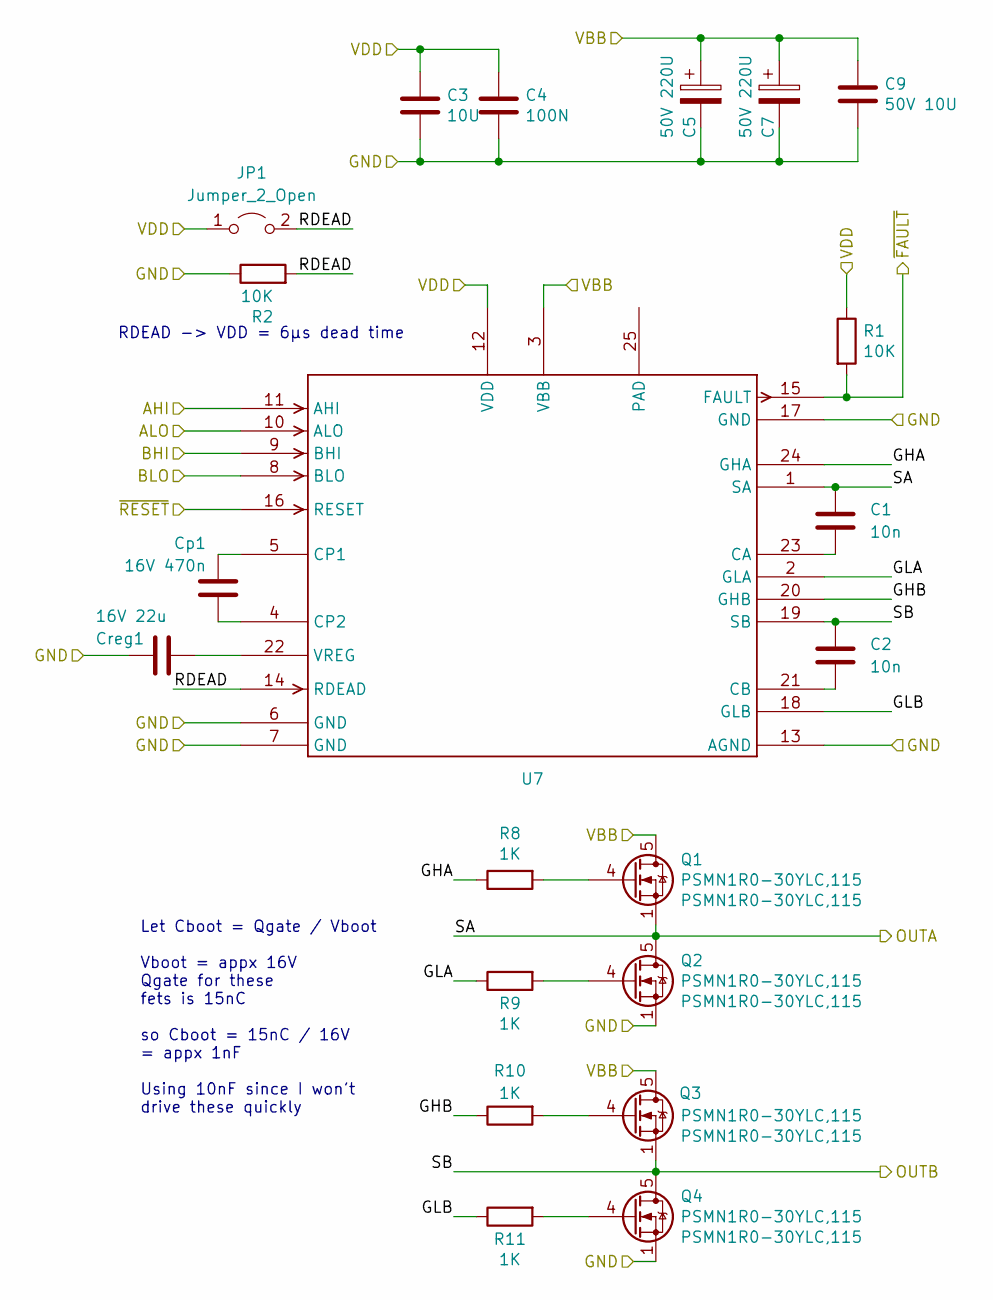
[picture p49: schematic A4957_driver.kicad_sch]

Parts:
C1, C2: 10n; C_0603_1608Metric
C3: 10U; C_0805_2012Metric
C4: 100N; C_0603_1608Metric
C5, C7: 50V 220U; CP_Elec_10x10
C9: 50V 10U; C_0805_2012Metric
Cp1: 16V 470n; C_0805_2012Metric
Creg1: 16V 22u; C_0805_2012Metric
JP1: Jumper_2_Open; R_0603_1608Metric
Q1, Q2, Q3, Q4: PSMN1R0-30YLC,115; LFPAK56; MPN PSMN1R0-30YLC,115
R1, R2: 10K; R_0603_1608Metric
R8, R9, R10, R11: 1K; R_0603_1608Metric
U7: HVQFN-24-1EP_4x4mm_P0.5mm_EP2.6x2.6mm_ThermalVias

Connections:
+5V: C3.1, C4.1, JP1.1 (A), R1.1, U7.12 (VDD); also elsewhere on the board
+BATT: C5.1, C7.1, C9.1, Q1.5 (D), Q3.5 (D), U7.3 (VBB); also elsewhere on the board
/A4957_driver/GHA: R8.1, U7.24 (GHA)
/A4957_driver/GHB: R10.1, U7.20 (GHB)
/A4957_driver/GLA: R9.1, U7.2 (GLA)
/A4957_driver/GLB: R11.1, U7.18 (GLB)
/A4957_driver/RDEAD: JP1.2 (B), R2.2, U7.14 (RDEAD)
/A4957_driver/~RESET: U7.16 (RESET)
/AHI: U7.11 (AHI); also elsewhere on the board
/ALO: U7.10 (ALO); also elsewhere on the board
/BHI: U7.9 (BHI); also elsewhere on the board
/BLO: U7.8 (BLO); also elsewhere on the board
/FAULT: R1.2, U7.15 (FAULT); also elsewhere on the board
/M1: C1.1, Q1.1 (S), Q1.2 (S), Q1.3 (S), Q2.5 (D), U7.1 (SA); also elsewhere on the board
/M2: C2.1, Q3.1 (S), Q3.2 (S), Q3.3 (S), Q4.5 (D), U7.19 (SB); also elsewhere on the board
GND: C3.2, C4.2, C5.2, C7.2, C9.2, Creg1.2, Q2.1 (S), Q2.2 (S), Q2.3 (S), Q4.1 (S), Q4.2 (S), Q4.3 (S), R2.1, U7.6 (GND), U7.7 (GND), U7.13 (AGND), U7.17 (GND); also elsewhere on the board
unnamed: Q1.4 (G), R8.2
unnamed: Q2.4 (G), R9.2
unnamed: Q3.4 (G), R10.2
unnamed: Q4.4 (G), R11.2
unnamed: C1.2, U7.23 (CA)
unnamed: C2.2, U7.21 (CB)
unnamed: Cp1.2, U7.5 (CP1)
unnamed: Cp1.1, U7.4 (CP2)
unnamed: Creg1.1, U7.22 (VREG)

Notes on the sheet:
Let Cboot = Qgate / Vboot Vboot = appx 16V Qgate for these fets is 15nC so Cboot = 15nC / 16V = appx 1nF Using 10nF since I won't drive these quickly
RDEAD -> VDD = 6µs dead time

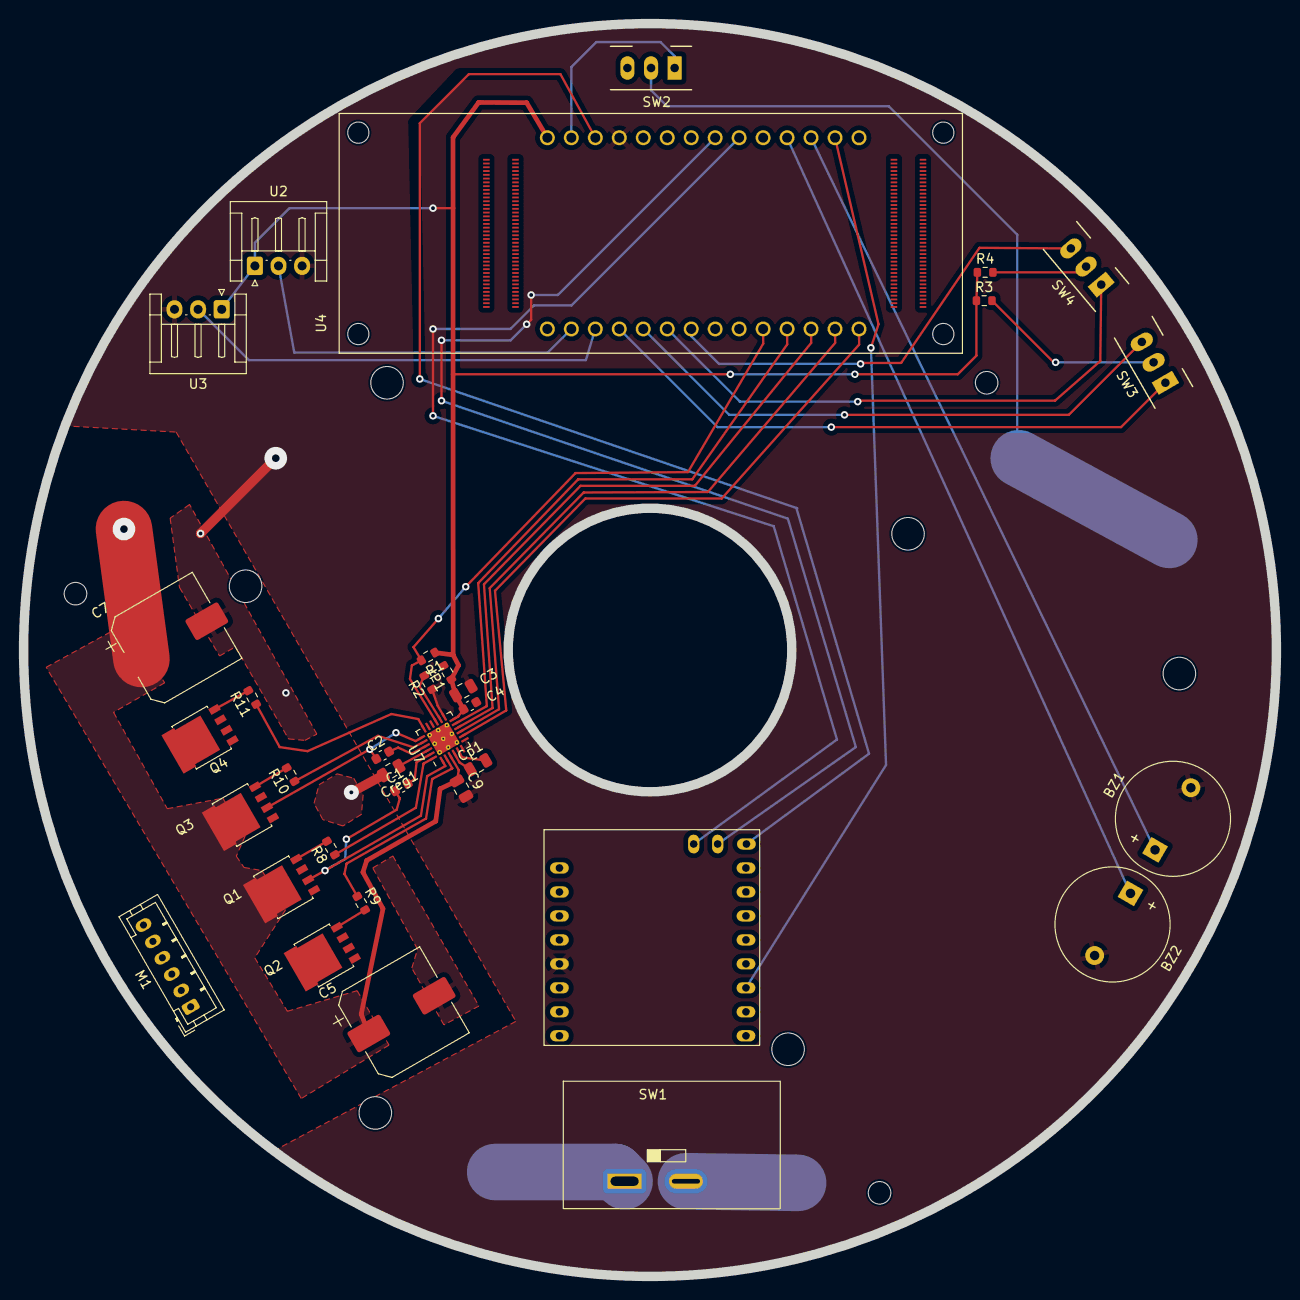
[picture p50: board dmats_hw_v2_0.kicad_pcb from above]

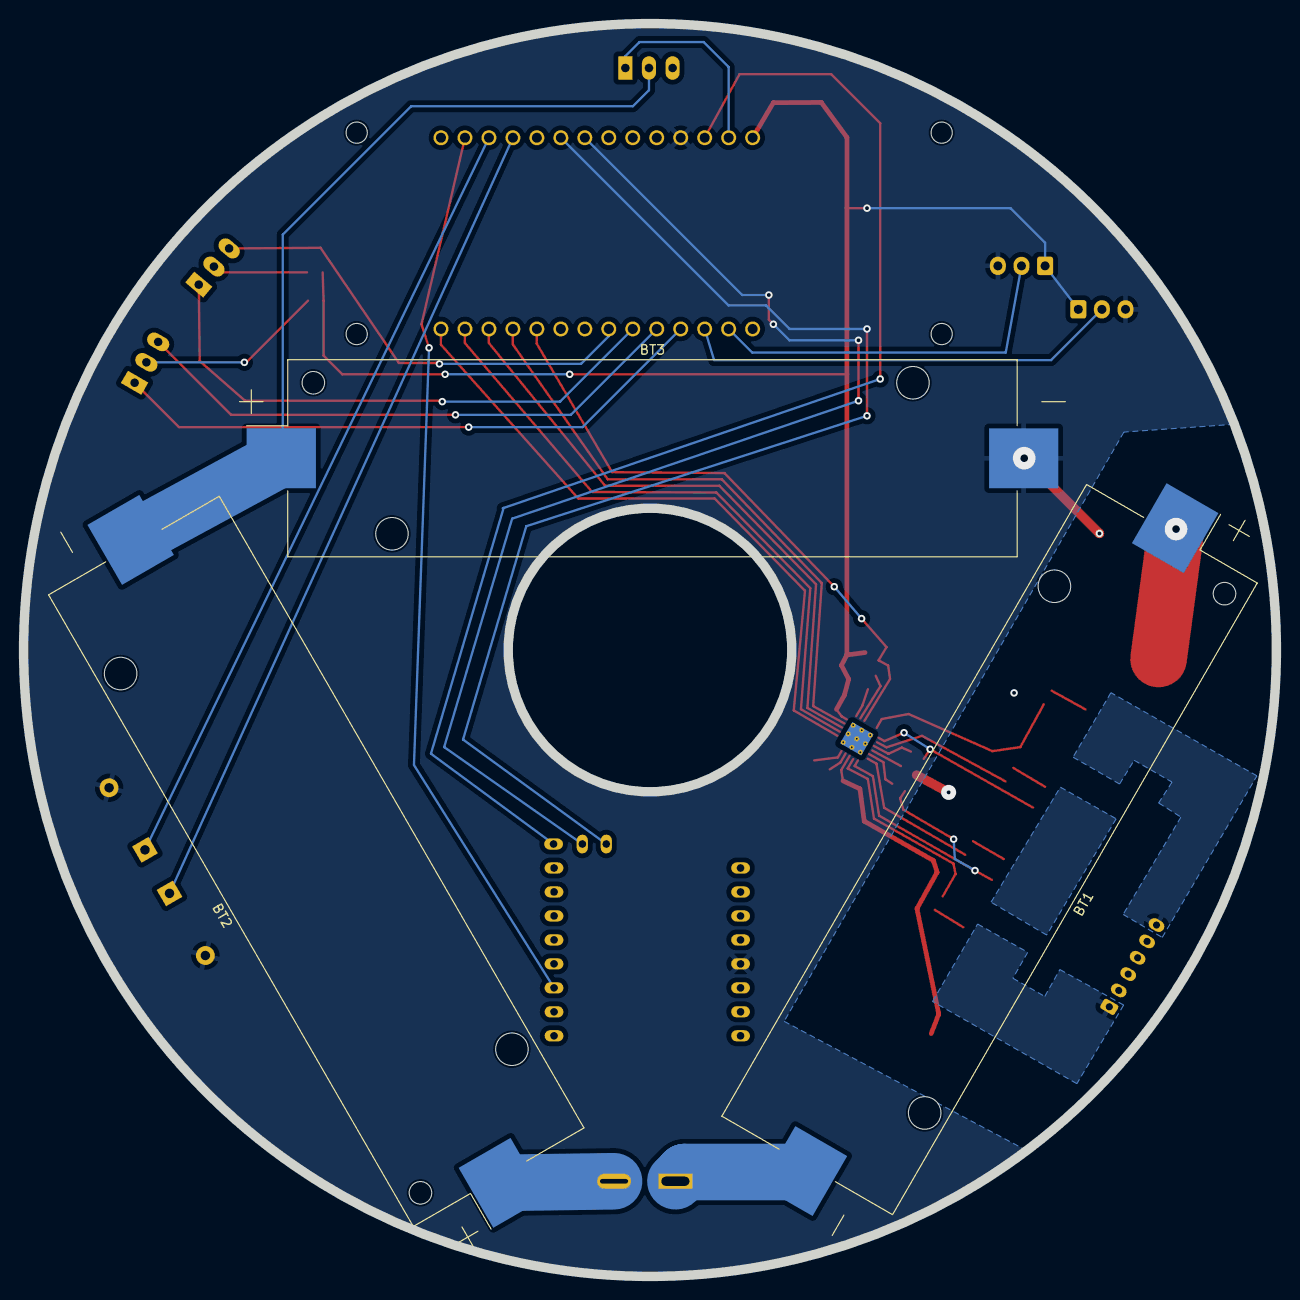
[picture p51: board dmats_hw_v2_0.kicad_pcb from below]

Board: 2 copper layers, 132.7 x 132.7 mm, 37 parts (3 on the bottom side), 47 nets.

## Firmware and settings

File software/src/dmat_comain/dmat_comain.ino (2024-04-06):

//#define ARDUINO_PORTENTA_H7_M7
//#define CORE_NUM_INTERRUPT 21

#include "Arduino.h"
#include "Arduino_BHY2Host.h"

#include "altitude.h"
#include "altitude_eqn/altitude_eqn.h"

#include <Encoder.h>
#include <PID_v1.h>
#include "DCMotorServo.h" // from https://github.com/CameronBrooks11/DCMotorServo

#define pin_dcmoto_encode1 0
#define pin_dcmoto_encode2 1
#define pin_dcmoto_dir1 2
#define pin_dcmoto_dir2 3
#define pin_dcmoto_pwm_out 4

// ESLOV - DO NOT USE
#define FORBIDDEN_PH8_I2C3_SDA 11
#define FORBIDDEN_PH7_I2C3_SCL 12
#define FORBIDDEN_PI0_SPI1_CS 7


// Encoder specifications
#define PPR 11 // Pulses per revolution (PPR) of the encoder
#define GEAR_RATIO 29 // Gear ratio of the gearbox. Change this according to your motor's gear ratio.

// Calculate Counts Per Revolution (CPR) for quadrature encoders
#define CPR (PPR * 4 * GEAR_RATIO)

DCMotorServo servo = DCMotorServo(pin_dcmoto_dir1, pin_dcmoto_dir2, pin_dcmoto_pwm_out, pin_dcmoto_encode1, pin_dcmoto_encode2);

// Define PID parameters as variables for easy adjustment
float KP = 0.1;
float KI = 0.15;
float KD = 0.05;


SensorXYZ accel(SENSOR_ID_ACC);
SensorOrientation ori(SENSOR_ID_ORI);
Sensor baro(SENSOR_ID_BARO);
SensorXYZ linaccel(SENSOR_ID_LACC);
SensorXYZ gyro(SENSOR_ID_GYRO);

AltBaro altBaro; // Barometer altitude estimator

struct vec3_t {
  float x;
  float y;
  float z;
};

// Altitude estimator
static AltitudeEstimator altitude = AltitudeEstimator(
        0.0005, // sigma Accel
        0.0005, // sigma Gyro
        0.018,   // sigma Baro
        0.5, // ca
        0.1);// accelThreshold

static void imuRead(float gyroData[3], float accelData[3])
{
      gyroData[0] = gyro.x()*PI/180.0/4096.0; // radians/second
      gyroData[1] = gyro.y()*PI/180.0/4096.0;
      gyroData[2] = gyro.z()*PI/180.0/4096.0;
      // and acceleration values
      accelData[0] = accel.x()/4096.0; // g-unit
      accelData[1] = accel.y()/4096.0;
      accelData[2] = accel.z()/4096.0;
}

float pastTime = millis();
float currentTime = millis();

bool printToggleFlag = false;
bool printFlag = false;


void setup() {
  // debug port
  Serial.begin(115200);
  while(!Serial);

  pinMode(pin_dcmoto_dir1, OUTPUT);
  pinMode(pin_dcmoto_dir2, OUTPUT);
  pinMode(pin_dcmoto_pwm_out, OUTPUT);
  pinMode(pin_dcmoto_encode1, INPUT);
  pinMode(pin_dcmoto_encode2, INPUT);

  servo.myPID->SetTunings(KP, KI, KD);
  servo.setPWMSkip(50);
  servo.setAccuracy(14); // Accuracy based on encoder specifics

  BHY2Host.begin();

  accel.begin();
  ori.begin();
  baro.begin();
  linaccel.begin();
  gyro.begin();
}


void loop()
{

  static unsigned long debug_timeout = millis();
  
  servo.run();
  
  if (millis() - debug_timeout > 1000) { // Every 1000ms, print debug info
    debug_timeout = millis();
    Serial.println(servo.getDebugInfo());
  }

  // Check if data is available to read
  while (Serial.available() > 0) {
    String command = Serial.readStringUntil('\n'); // Read the command until a newline character
    command.trim(); // Remove any whitespace or newlines

    // Parse PID tuning commands
    if (command.startsWith("KP=")) {
      KP = command.substring(3).toFloat();
      servo.myPID->SetTunings(KP, KI, KD);
      Serial.print("KP set to: ");
      Serial.println(KP);
    }
    else if (command.startsWith("KI=")) {
      KI = command.substring(3).toFloat();
      servo.myPID->SetTunings(KP, KI, KD);
      Serial.print("KI set to: ");
      Serial.println(KI);
    }
    else if (command.startsWith("KD=")) {
      KD = command.substring(3).toFloat();
      servo.myPID->SetTunings(KP, KI, KD);
      Serial.print("KD set to: ");
      Serial.println(KD);
    }else if (command.startsWith("MOVE=")) {
      String value = command.substring(5); // Extract the command value
      if (value == "1R") {
        // If the command is to rotate one full revolution
        servo.move(CPR); // Move the motor by one full revolution based on CPR
        Serial.println("Rotating one full revolution");
      } else {
        int newPosition = value.toInt(); // Try to convert to integer for custom moves
        if (newPosition != 0) {
          servo.move(newPosition); // Move the motor to the new position
          Serial.print("Moving to: ");
          Serial.println(newPosition);
        } else {
          Serial.println("Invalid MOVE command");
        }
      }
    }
    else if (command.startsWith("MAXPWM=")) {
      int maxPWM = command.substring(7).toInt(); // Extract and convert max PWM value to integer
      if (maxPWM >= 0 && maxPWM <= 255) {
        servo.setMaxPWM(maxPWM); // Set the maximum PWM value
        Serial.print("Setting MAXPWM to: ");
        Serial.println(maxPWM);
      } else {
        Serial.println("Invalid MAXPWM command");
      }
    } else {
      Serial.println("Invalid command");
    }
  }


// --------------------------

  BHY2Host.update();

  // Check for serial input to toggle printToggleFlag
  if (Serial.available() > 0) {
    String command = Serial.readStringUntil('\n'); // Read the command until a newline character.
    command.trim(); // Trim any whitespace.

    if (command.equals("toggle")) { // If the command is "toggle", invert the printToggleFlag state.
      printToggleFlag = !printToggleFlag;
      Serial.println(printToggleFlag ? "Printing Enabled" : "Printing Disabled"); // Feedback.
    }
  }  

  currentTime = millis();
  

  if ((currentTime - pastTime) > 50 && !printToggleFlag && printFlag)
  {
    // get all necessary data
    float pressure = baro.value();
    altBaro.update(pressure);
    float baroHeight =  altBaro.getAltitude();
    uint32_t timestamp = micros();
    float accelData[3];
    float gyroData[3];
    imuRead(gyroData, accelData);
    altitude.estimate(accelData, gyroData, baroHeight, timestamp);
    Serial.print("Altitude Estimator: ");
    Serial.print(baroHeight);
    Serial.print(",");
    Serial.print(altitude.getAltitude());
    Serial.print(",");
    Serial.print(altitude.getVerticalVelocity());
    Serial.print(",");
    Serial.println(altitude.getVerticalAcceleration());
    pastTime = currentTime;
  }



  static auto printTime = millis();
  if (millis() - printTime >= 500 && printToggleFlag && printFlag) {
    printTime = millis();
    Serial.println(String("Acceleration values: ") + accel.toString());
    Serial.println(String("Orientation values: ") + ori.toString());
    Serial.println(String("Barometer value: ") + baro.toString());
    Serial.println(String("Linear Acceleration: ") + linaccel.toString());
    printSerialwUnits();
  }


}


void printSerialwUnits()
{
    // Measure state:  
  vec3_t linaccel_data = { linaccel.x()/4096.0, linaccel.y()/4096.0, linaccel.z()/4096.0};    // g-unit
  vec3_t gyro_data = { gyro.x()*PI/180.0/4096.0, gyro.y()*PI/180.0/4096.0, gyro.z()*PI/180.0/4096.0};     // radians/second

  // Print linear acceleration data with units
  Serial.print("Linear Acceleration X: ");
  Serial.print(linaccel_data.x, 6); // Assuming 6 decimal places for precision
  Serial.print(" g, Y: ");
  Serial.print(linaccel_data.y, 6);
  Serial.print(" g, Z: ");
  Serial.print(linaccel_data.z, 6);
  Serial.println(" g");

  // Print gyro data with units
  Serial.print("Gyro Data X: ");
  Serial.print(gyro_data.x, 6); // Assuming 6 decimal places for precision
  Serial.print(" rad/s, Y: ");
  Serial.print(gyro_data.y, 6);
  Serial.print(" rad/s, Z: ");
  Serial.print(gyro_data.z, 6);
  Serial.println(" rad/s");

}

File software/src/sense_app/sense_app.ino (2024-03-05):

/* 
 * Use this sketch if you want to control nicla from 
 * an external device acting as a host.
 * Here, nicla just reacts to external stimuli coming from
 * the eslov port or through BLE 
 * 
 * NOTE: Remember to choose your Nicla configuration! 
 * If Nicla is used as a Shield, provide the NICLA_AS_SHIELD parameter.
 * If you want to enable just one between I2C and BLE,
 * use NICLA_I2C or NICLA_BLE parameters.
 *
*/

#include "Arduino.h"
#include "Arduino_BHY2.h"

// Set DEBUG to true in order to enable debug print
#define DEBUG false

void setup()
{
#if DEBUG
  Serial.begin(115200);
  BHY2.debug(Serial);
  BHY2.setLDOTimeout(60000);
#endif

  BHY2.begin();
}

void loop()
{
  // Update and then sleep
  BHY2.update(100);
}

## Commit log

2023-10-16 Added flaps taking time to deploy to PID simulation
2023-10-17 New folder for prelim flight analysis
    [2022-06-24-serial-5115-flight-0001.csv, 2022-06-24-serial-6583-flight-0003.csv]
2023-10-18 added sensor / board documentation & design files
    [4816 BMP390 QT.f3d, 4816 BMP390 QT.step, 4816 BMP390 QT.stl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]
2023-10-20 minor changes
    [2022-06-24-serial-5115-flight-0001.csv, 2022-06-24-serial-6583-flight-0003.csv]
2023-12-05 added electrical schematic start and resources
    [4816 BMP390 QT.f3d, 4816 BMP390 QT.step, 4816 BMP390 QT.stl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]
2024-01-11 rename sim folder
    [2022-06-24-serial-5115-flight-0001.csv, 2022-06-24-serial-6583-flight-0003.csv]
2024-01-15 launch rail length now accounts for added DOFs when only one launch lug left on rail (almost negligeable change ~10ft)
2024-01-18 did some refactoring of sims and repo structure
    [4816 BMP390 QT.f3d, 4816 BMP390 QT.step, 4816 BMP390 QT.stl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]
2024-01-18 Added STEP Files
    [Flap Support.STEP, Flap.STEP, Lead Screw.STEP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]
2024-01-19 Added Assemblies at different Angles
2024-01-20 updated analyses, an attempt at trying out servo and updated sims
2024-01-20 updated analyses, an attempt at trying out stepper and updated sims
2024-01-26 renamed "launch lug" to "rail button" (because that's what they are)
2024-02-09 updated pressures and temperatures used in sensitivity analysis
2024-02-10 added stopping power analysis
2024-02-11 added battery design work
    [18650_Holder.scad, battery_assem-x1.scad, battery_assem-x1.stl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]
2024-02-12 - option for variations in sensitivity analysis to be drawn from a gaussian instead of just a linspace - added wind correction (flat -300 ft) to stopping power sim
2024-02-16 optimizations to sim: - default timestep of simulation (with and without airbrakes) now 0.01 instead of 0.001 (they only differ by about 2m in apogee) - brought conversion to radians of parameters de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
2024-02-20 - cleaned up - fixed TeleMega data in visualizations_cleaned
    [2022-06-24-serial-5115-flight-0001.csv, 2022-06-24-serial-6583-flight-0003.csv]
2024-02-21 - added RocketPy sim - refactored classes, now have motor class
2024-02-21 - added Prometheus RocketPy sim - some organization
    [2022-06-24-serial-5115-flight-0001.csv, 2022-06-24-serial-6583-flight-0003.csv]
2024-02-27 added some more stuff for motor analysis
2024-03-10 added electrical schematic
    [aeris_freni_v1_0.kicad_pcb, aeris_freni_v1_0.kicad_sch]
2024-03-12 added software libs
    [4816 BMP390 QT.f3d, 4816 BMP390 QT.step, 4816 BMP390 QT.stl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]
2024-03-12 - fixed outdated static call of flap area in load analysis within flight-simulator directory - cleanup -added ideas, TODOs to track what still needs doing - various minor changes
2024-03-14 Added a more precise temperature lapse rate
2024-03-18 motor servo software updates
    [Linear Magnetic Hall Effect Switches.SLDASM, MOTOR_DRIVER_L298N.SLDPRT]
2024-03-31 made first lookup table
    [burnout_states.csv]
2024-03-31 changed lookup table location
    [burnout_states.csv]
2024-03-31 changed lookup table directory to flight-simulator
    [burnout_states.csv]
2024-04-02 software tweaks and development of A4957 custom driver
    [A4957_driver.kicad_sch, dmats_hw_v1_0.kicad_sch, dmats_hw_v2_0.kicad_pcb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]
2024-04-02 v2 of circuit for PCB
    [A4957_driver.kicad_sch, dmats_hw_v2_0.kicad_sch]
2024-04-03 created all PCB footprints
    [A4957_driver.kicad_sch, dmats_hw_v2_0.kicad_sch, portenta_h7.kicad_sch]
2024-04-04 bulk of PCB design layout complete
    [A4957_driver.kicad_sch, dmats_hw_v2_0.kicad_pcb, dmats_hw_v2_0.kicad_sch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]
2024-04-04 PCB work
    [A4957_driver.kicad_sch, dmats_hw_v2_0.kicad_pcb]
2024-04-05 completed motor driver PCB
    [dmats_hw_v2_0.kicad_pcb, dmats_hw_v2_0.kicad_sch]
2024-04-06 software dir refactoring before flight computer merge
    [dmats_hw_v2_0.kicad_pcb]
2024-04-08 rewrote sim, classes, and other scripts to take Cd as a function of Ma instead of Re
    [burnout_states.csv]
2024-04-09 sim updates for force analysis and visual clean up on elec drawings
    [A4957_driver.kicad_sch, dmats_hw_v1_0.kicad_sch, dmats_hw_v2_0.kicad_pcb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]
2024-04-09 Initial commit splitting capstone repo
    [18650_Holder.scad, 2022-06-24-serial-5115-flight-0001.csv, 2022-06-24-serial-6583-flight-0003.csv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]
2024-04-20 transfer and beef up of documentation
    [18650_Holder.scad, 2022-06-24-serial-5115-flight-0001.csv, 2022-06-24-serial-6583-flight-0003.csv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]
2024-04-20 Configure LFS to track SolidWorks, STEP, and STL files
2024-04-21 minor documentation updates
    [burnout_states.csv]
2024-04-24 added a few things from Teams, minor fixes to docs
    [Mould Base.STEP, Mould Top.STEP]
2024-05-22 updated to use rocketflightsim as a package
    [burnout_states.csv]
2024-06-08 updates of configs with new masses, updates of sims, start of new advanced lookup table generation
    [burnout_states.csv]
2024-07-05 addition of Hyperion flight data
    [2024-06-21-serial-6583-flight-0004.csv]
